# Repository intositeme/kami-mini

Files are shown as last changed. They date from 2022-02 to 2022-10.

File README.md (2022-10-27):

# Kami Mini extruder

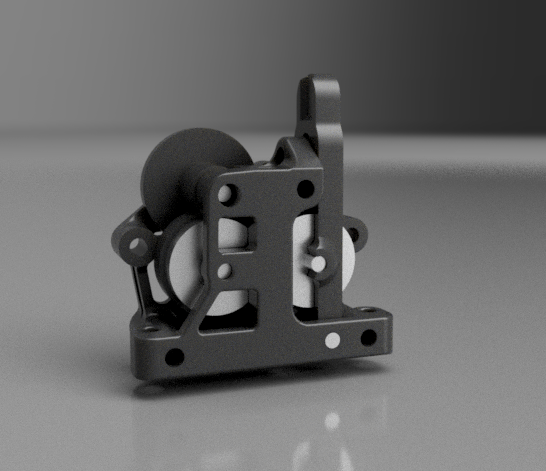
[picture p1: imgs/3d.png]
Image of Extruder


## An extruder using Bondtech™ LGX gears

Heavily inspired by the [Sherpa Mini](https://github.com/Annex-Engineering/Sherpa_Mini-Extruder) by [Annex Engineering](https://github.com/Annex-Engineering/)

Same attachment spacing and filament path as the Sherpa Mini therefore you can reuse your current tool mount along with PTFE tubes.

## Bill of Materials (BOM)

### Common hardware
- 4x M3x5x4mm heat inserts
- 2x M3x12mm ISO 7380 button head screws
- 3x M3x25mm ISO 7380 button head screws
- Bondtech BMG Thumbscrew Tensioner
- Latch Arm axle:
   - 3x20mm dowel pin

   or

   - 1x M3x5x4mm heat inserts
   - 1x M3x25mm ISO 7380 button head screw

### Bondtech™ LGX parts
Either scavenge the LGX or LGX lite for parts or:
- 1x [LGX® Primary Gear](https://www.bondtech.se/product/lgx-primary-gear/)
- 2x [LGX® Secondary Gear](https://www.bondtech.se/product/lgx-secondary-gear/)
- 2x [LGX® Hardened Steel Drive Wheel](https://www.bondtech.se/product/lgx-hardened-steel-drive-wheel/)
- 2x [Needlebearing](https://www.bondtech.se/product/needlebearing/)
- 2x 3x16mm dowel pins
- 1x 3x20mm dowel pin

### Stepper
1x Nema 14 36mm Pancake Stepper - 10T (T=Teeth) or 8T it's up to you, good choices are high temp models:
 - MOONS' CSE14HRA1L410A
 - LDO-36STH17-1004AHG

## Notes
The model is prepared for using 4 (+one optional for Latch Arm axle using screw instead of pin) M3x5x4 heat inserts. They can be brought in any decent 3d printing eshop (eshops selling parts for Voron usually sells these).

Latch Arm combined with Thumbscrew Tensioner should provide enough of grip on filament. However the latch frame is thin arounfd the gearings (design issue) and could [break](imgs/BrokenLatchArm.jpg). Solutions (in order of success):
 - Print the Latch Arm from filament enriched with CF (I am using Prusament PC CF with great success).
 - Aneal it after printing to further improve layer bonding.
 - You cound try to print it rotated by 90° (requires supports) thus the layers are positioned perpendicular to tensioning force.

## Print Settings
Use ABS or ASA if posssible. It depends on whever you will be using the Extruder. PLA or PETG is not suitable in enclosed chamber. Or even better use PC CF (see info above).
The STL's are already oriented for you, so you only need to send them to the slicer.
There is no need for supports; recommended settings are 4 perimeters/top/bottom, at least 30% infill. You might consider rotating 90° the Latch Arm to combat the issue mentioned in [Notes](#Notes).

## Assembly
See the [assembly.md](assembly.md).

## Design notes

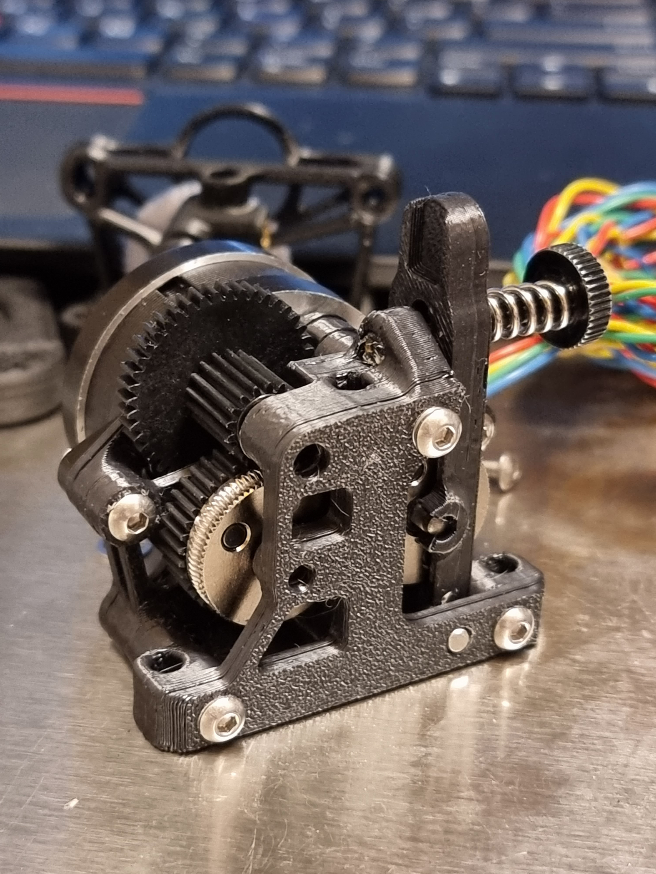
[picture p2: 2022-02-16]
imgs/pht.jpg

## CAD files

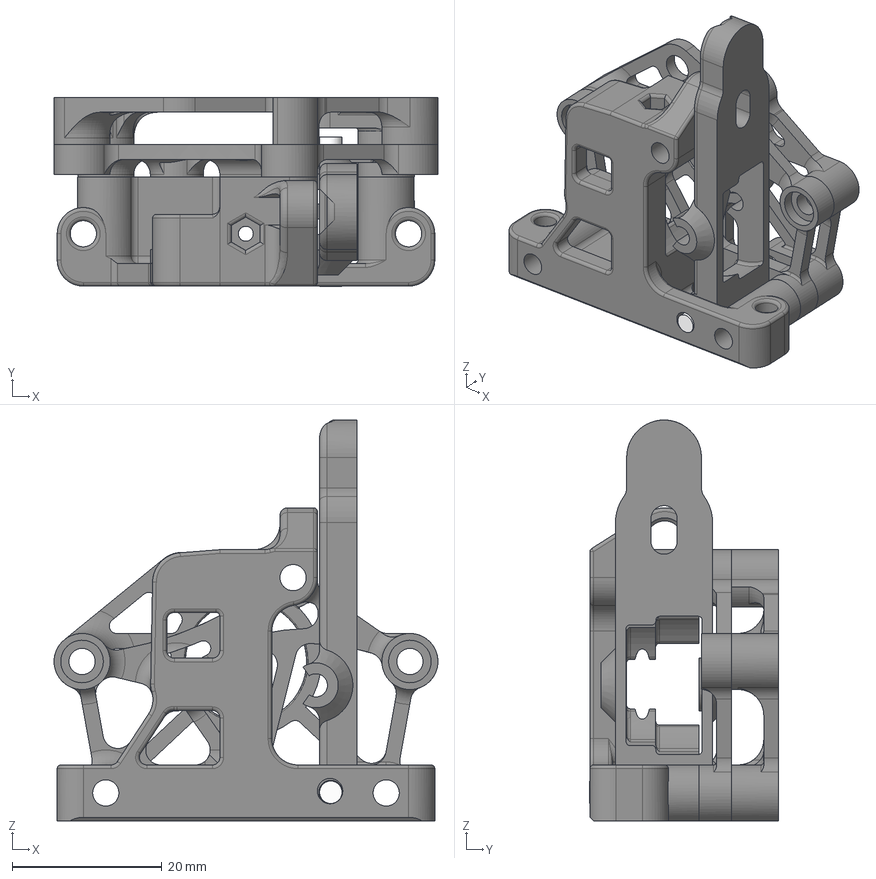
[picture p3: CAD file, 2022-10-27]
cad/Kami Mini.step
51.3 x 25.3 x 53.6 mm
Back Plate
Latch Pin
Mid Plate
Front Plate

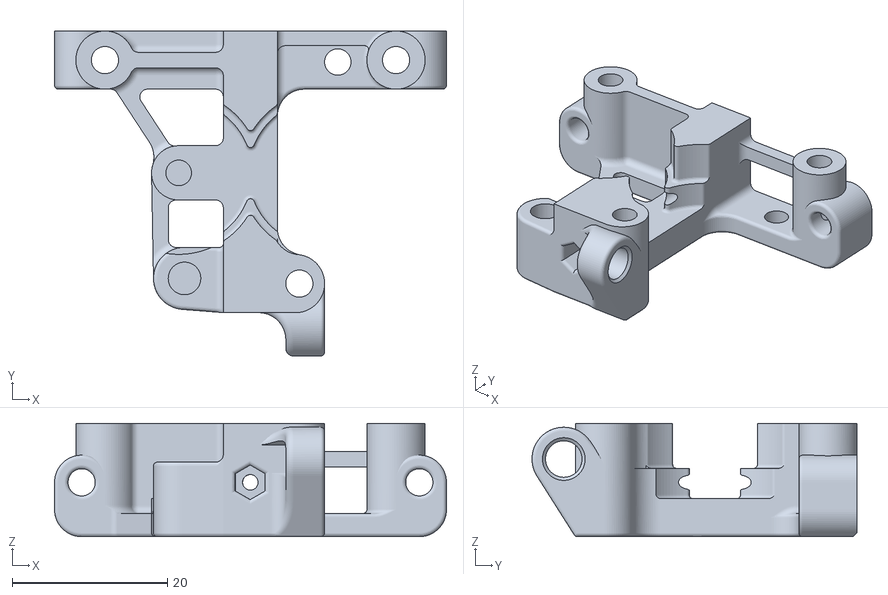
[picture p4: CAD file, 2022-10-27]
stls/Front_Plate.stl
50.5 x 41.9 x 14.6

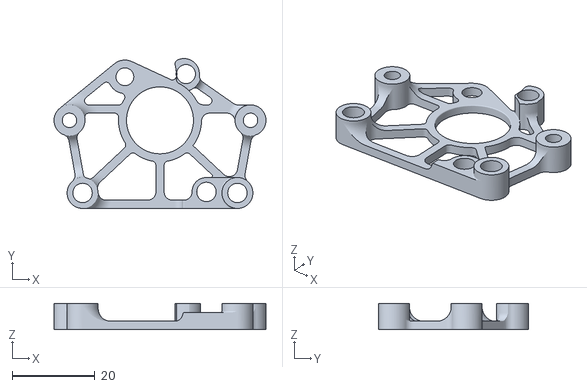
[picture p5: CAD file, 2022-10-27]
stls/Back_Plate.stl
51.3 x 36.3 x 6.30

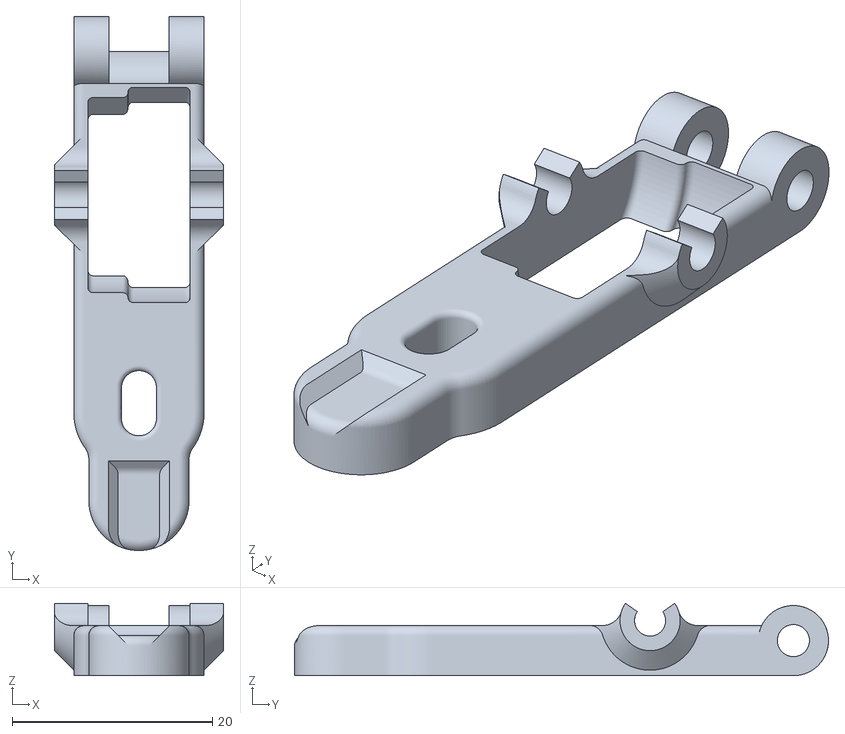
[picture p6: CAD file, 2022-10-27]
stls/Tension_Gear_Latch.stl
16.9 x 53.3 x 7.22

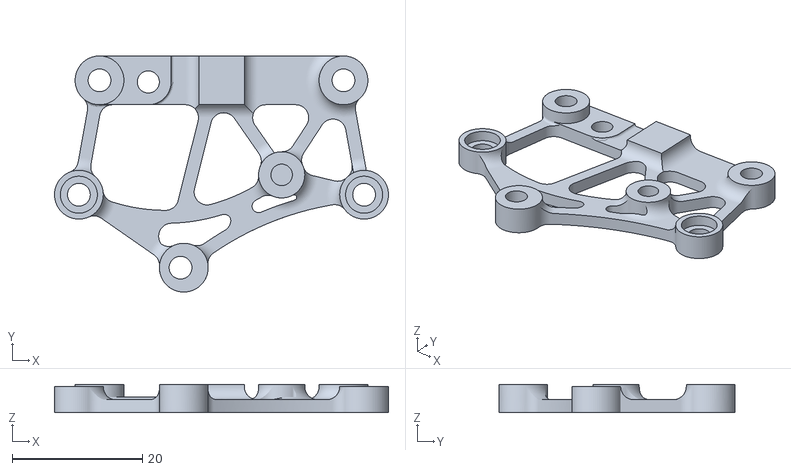
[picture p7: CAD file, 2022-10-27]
stls/Mid_Plate.stl
51.3 x 36.3 x 4.35

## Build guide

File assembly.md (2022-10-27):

# Assembly

If you haven't scavenged LGX (lite) extruder for parts then you have to first assemble the LGX gearings. Otherwise skip to step 2.

1) LGX Gearings:
   - Combine both Secondary Gear with Hardened Steel Drive Wheel. Then carefuly insert the Needlebearing into Secondary Gearing and finaly slide in the 16mm dowel pin.

2) Front Plate:
   - Start with front plate by laying it on the desk outer side down. Insert one Secondary Gearing on the right side.
   - Using slight force press fit the other Secondary Gearing into the Latch Arm. Slide the 20mm dowel pin into the holes at the bottom of Latch Arm and insert it to the front face on the left saligning it with the Secondary Gear's teeths. Or if not using the dowel pin slide from front in the M3x25mm screw and onto screw slide the Latch Arm with gearings.
   - Insert heatset into the front plate from the oposite side than the latch is located. This way the insert gets seated more firmly in the plastic thus reducing the risk of being pulled out when the Thumbscrew Tensioner is screwed in. 
   Speaking of which screw in the Thumbscrew Tensioner a bit to hold the Latch Arm in place for the rest of the assembly.

3) Middle Plate:
   - On top of the stack put the Middle Plate so that flush side is facing towards you.
   - Slide the 20mm dowel pin into Primary Gear. Then put it with smaller gear first into the Front Plate and align the teeth with right Secondary Gearing.

4) Back Plate:
   - Set the Back Plate with flush side towards you on the desk.
   - Push in the heat inserts into bottom outer holes. If using the screw as Latch Arm axle also put the heatset insert into the hole next to the bottom left one.
   - ⚠️ Top heat insert on Back Plate has only 2/3 of plastic around it. Be careful with inserting it and try force out as little plastic as possible (should go in without forcing out any material). After installing insert, check that it is not interferring with the Primary Gear. You might need to trim the execess plastic down.
   - Then with Primary Gear pin acting as positioner guide put the Back Part on top the stack with flush side facing towards you.

     The results should look like this:back plate assembly

5) Put on top oth the stack the Nema 14 Pancake Steeper aligned with Primary Gear teeth.

6) Hold front and back of the whole assembly between two fingers and flip it with front side towards you. Scew two M3x12mm all the way into the Stepper (two holes at the sides in the middle row). Now the assembly should held together and is much easier to work with. Screw two M3x25mm at the bottom (on both sides) into the Back Plate inserts. If using screw as Latch Arm axle screw it into its insert too. Lastly screw one M3x25mm into the topmost insert.

## Assembly Checks
- [❓] Check that all the gearings moves properly without any grindinding (especially mind the partialy held insert).
- [❓] Try to insert the filament and check if it slides through the whole filament path with ease. You might need to clear the path from excess plastic with 2mm drill.
- [❓] Check how well the latch aligns within boundaries of gearings when press tightened using Thumbscrew Tensioner and loaded filament.

And that's all folks.

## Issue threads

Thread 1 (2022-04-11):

Mid Plate missing in CAD

MAD-HATMAN, 2022-04-11:
Hello,

Thank you for sharing!
Is it possible to have the mid plate in the CAD file please?

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

jeralm, 2022-04-18:
I'm also interested

issic, 2022-10-02:
Yep the same

intositeme, 2022-10-27:
Sorry, didn't realised it was missing from the CAD when i exported it from Fusion. Haven't been watching this and am not active on Discord.

Merged @cuiviemen updates which mentions the mid plate. Haven't checked the files though.

cuiviemen, 2022-10-27:
Yep my PR #2 does contain in step file the retraced (from stl) mid plate.

Closed 2022-10-27.

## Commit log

2022-02-16 Uploaded STLs
    [Back Plate.stl, Front Plate.stl, Mid Plate.stl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]
2022-02-19 Covered primary gear shaft mounting hole.
    During print, due to gear using bushing and not bearings, constant extruding will cause the shaft to ride out of the rear mounting hole. Covered front hole so the shaft is held in place
    [Front Plate.stl]
2022-05-28 Updated .step file with QoL changes and retraced Mid_Plate.
    [Kami Mini.step]
2022-05-28 Updated QoL .stl files (with proper orientation).
    [Back_Plate.stl, Front_Plate.stl, Mid_Plate.stl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]
2022-05-29 Add more informations (BOM, assembly) to the README.
2022-05-29 Streamlined assembly.md. Fixed typos.
